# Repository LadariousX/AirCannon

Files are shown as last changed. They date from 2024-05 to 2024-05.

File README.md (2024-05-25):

# AirCannon
Repo for my recent air cannon project.



https://github.com/LadariousX/AirCannon/assets/42398415/c019e453-44b1-493c-81a6-e544174ef49f

This project is not for beginners... I'm no expert and I'm able to tell you not eveything went perfectly. I didnt even weld this one. That being said It came out nice but still you should have a strong basis in the followeing skills before attempting this project: Stainless welding (and other metalworking), 3d printing, CAD.

This project cost me near $300 R&D included your price will vary, heres the expenditures:
Don't forget to shop around these links are only reference!
| disc | 🔗 | 💰 | notes |
|---|---|----|---|
| Stainless fire extinguisher | 🧯 | 0.00 | recharge facility, out of cert |
| 1.5" full port ball valve | [link](https://www.directmaterial.com/brass-ball-valve-full-port-600-psi-wog) | 26.50 |
| 1.5 NPT x 10" pipe | [link](https://www.mcmaster.com/4549K664/) | 12.00 | 
| MH Build PETG | [link](https://www.matterhackers.com/store/c/3d-printer-filament/mh-build-series-petg) | 21.98 |ABS or machined lylon may work too|
| HM Build TPU | [link](https://www.matterhackers.com/store/c/mh-build-series-tpu)| 28.99 |
| 1/16" Coated steel cable | [link](https://www.homedepot.com/p/Everbilt-1-16-x-1-ft-Galvanized-Vinyl-Coated-Steel-Wire-Rope-in-Green-806376/204630484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) | 2.00 | Primary spring cable |
| (small) Coated steel cable | 🤷‍♂️ | 6.00| I used fishing leader|
| Misc Crimps | 🤷‍♂️ | 2.00 | cable crimps |
| 3/16" Brake line | 🤷‍♂️ | 10.00 | sleave for trigger linkage |
| Primary spring | 🤷‍♂️ | 🤪 | I slavaged mine from a dishwasher. |
| Trigger return spring | 🤷‍♂️ | 3.00 | choose to fit |
| Bering | [link](https://www.mcmaster.com/60355K336/) | 7.72 | McMasterCarr link... you can buy anywhere|
| .25 UNC x.75" socket head | [link](https://www.mcmaster.com/91274A164/) | 12.05 | Stainless not necessary but helps |
| .25" UNC nylon lock nut | [link](https://www.mcmaster.com/90715A125/) | 8.95 |
| M3x25 socket head | [link](https://www.mcmaster.com/91292A020/) | 8.72 |
| M3 nut | [link](https://www.mcmaster.com/91828A211/) | 4.73 |
| 1/4" NPT Guage| [link](https://www.mcmaster.com/4000K791-4000K565/) | 15.85 |
| Teflon / PTFE tape | [link](https://www.mcmaster.com/6802K33/) | 5.37 | 
| Misc air fittings | 🤷‍♂️ | 20.00 | m&f 1/4" NPT bung, valve, connector... |
| Por15 sealer | [link](https://por15.com/collections/fuel-tank-restoration/products/fuel-tank-sealer) | 18.38 | seal pinholes |

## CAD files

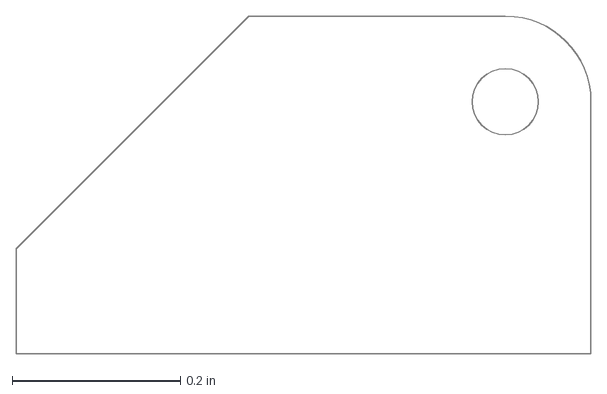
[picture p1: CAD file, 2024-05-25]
DXF cuts/125 rel spring anchor.dxf
0.684 x 0.402 in

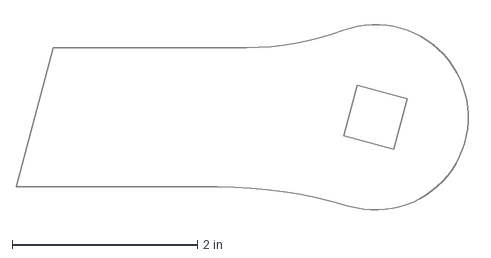
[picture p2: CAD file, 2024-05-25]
DXF cuts/furniture/125 Forwatd handle riser.dxf
4.95 x 2.17 in

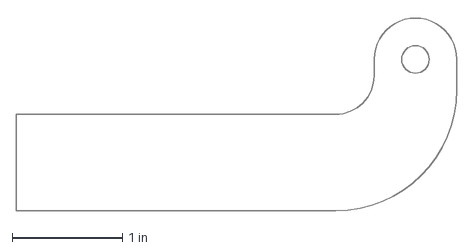
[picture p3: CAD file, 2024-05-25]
DXF cuts/rel sys/125 rel claw arm.dxf
4.00 x 1.77 in

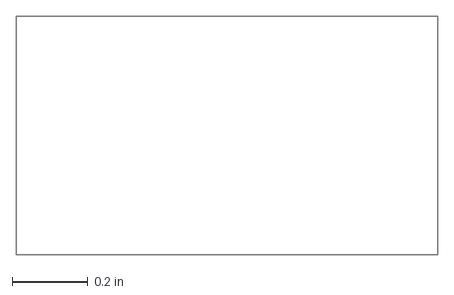
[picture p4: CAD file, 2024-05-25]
DXF cuts/tank inlet body/125 inlet back.dxf
1.11 x 0.63 in

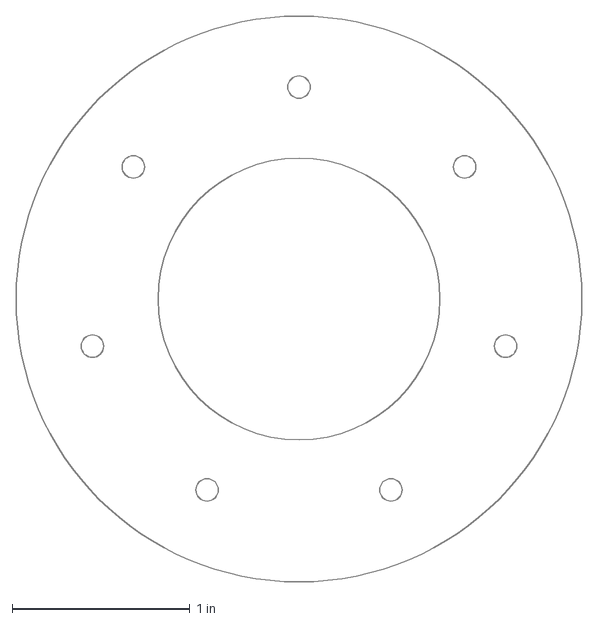
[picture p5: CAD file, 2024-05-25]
DXF cuts/trigger cam stack/16ga stack upper.dxf
3.19 x 3.19 in

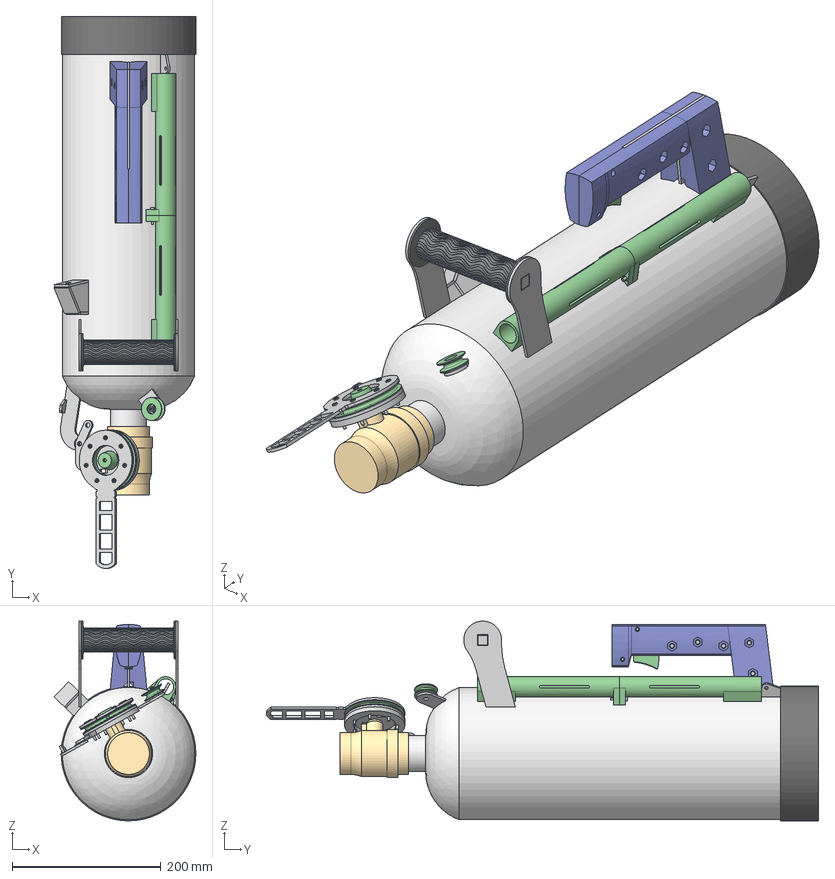
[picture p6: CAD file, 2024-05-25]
potato luancher Master.step
190.5 x 741.1 x 268.2 mm
inlet
hole saw align
Valve body
lower
track
Broached Hexagon Socket Head Cap Screw ANSI B18.3.1M - M3x0.5 x 25 St eel Grade 2 Zinc v1 x 7
trigger cam
arming lever
F handle riser L
F handle riser L(Mirror)
Socket Head Cap Screw JIS B 1176 - M3 x 0.5 x 20 Steel 4.6 Plain v1 x 2
spring anchor
handle body
trigger
Aft handle reinforcement
spacer
pully arm
spring pully
claw
Release arm
bushing
Hexagon Socket Head Cap Screw ANSI B18.3 - 1/4-28 UNF x 0.75 Steel Gr ade 2 Plain v1 x 5

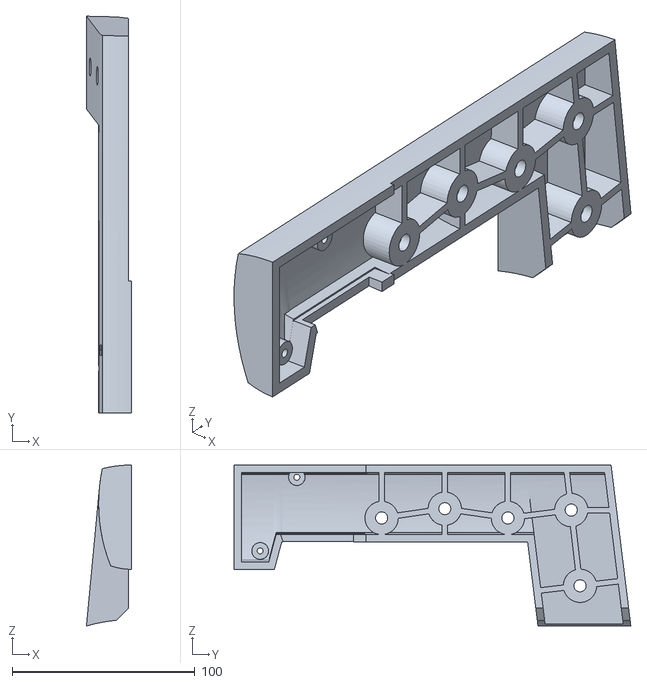
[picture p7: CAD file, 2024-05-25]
STL/aft handle/aft handle right.stl
24.7 x 216.9 x 88.0

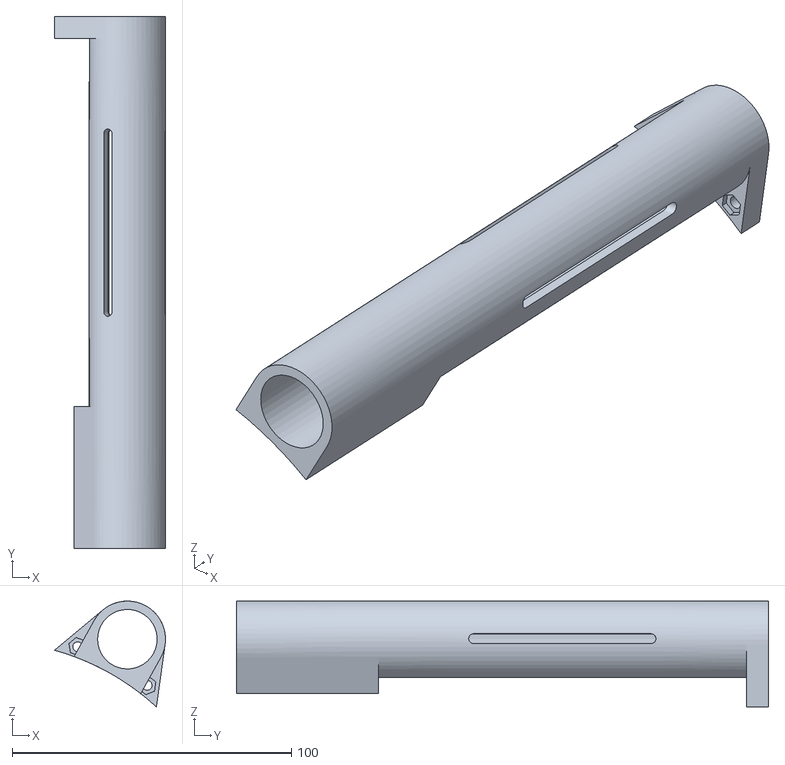
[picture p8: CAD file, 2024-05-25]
STL/buffer tube/buffer tube upper.stl
39.7 x 190.5 x 37.9

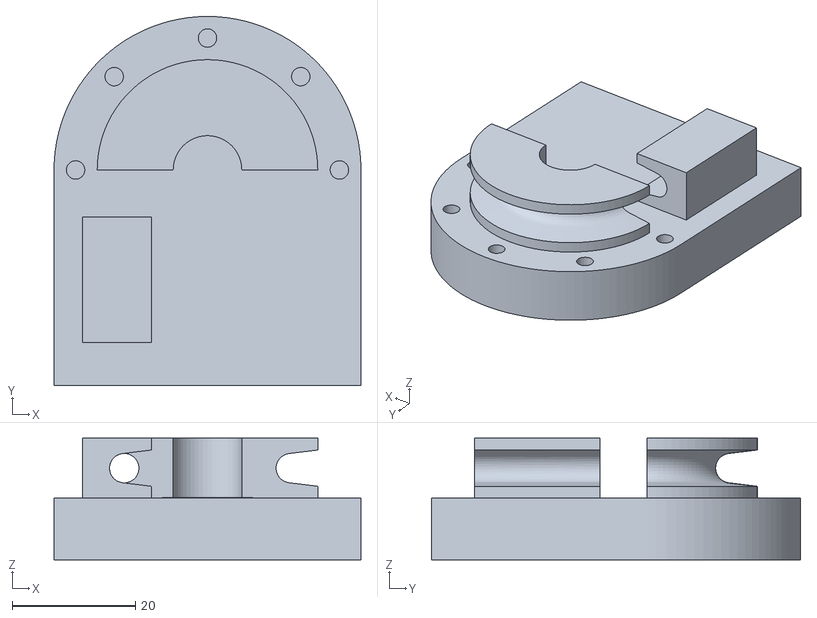
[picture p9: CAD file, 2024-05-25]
STL/jigs & alignment/tubing bender.stl
49.8 x 59.8 x 19.7

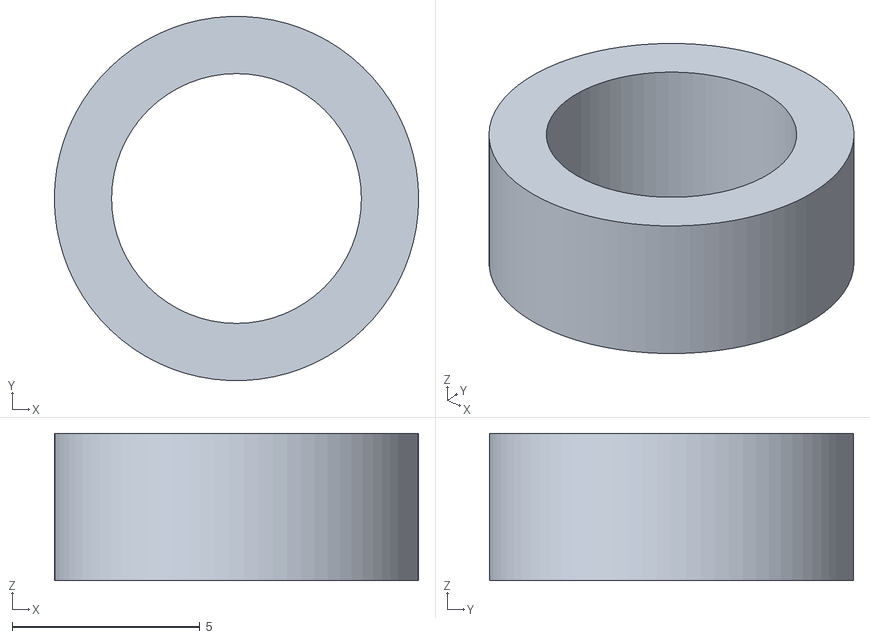
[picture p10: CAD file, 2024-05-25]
STL/Primary spring sys/primary pully 1 spacer.stl
9.70 x 9.69 x 3.91

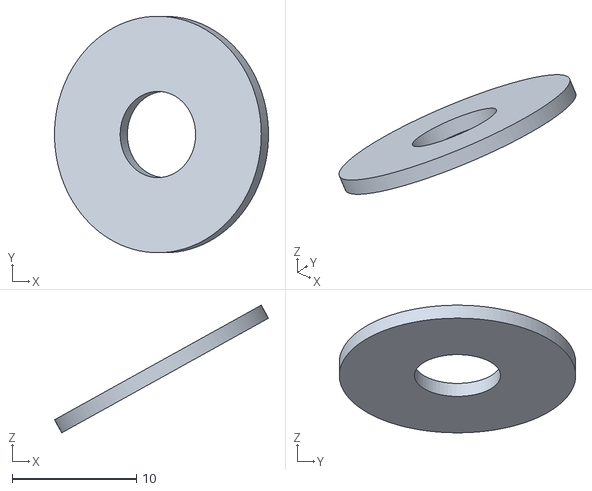
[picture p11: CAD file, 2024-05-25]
STL/rel claw bushing.stl
17.2 x 19.0 x 10.3

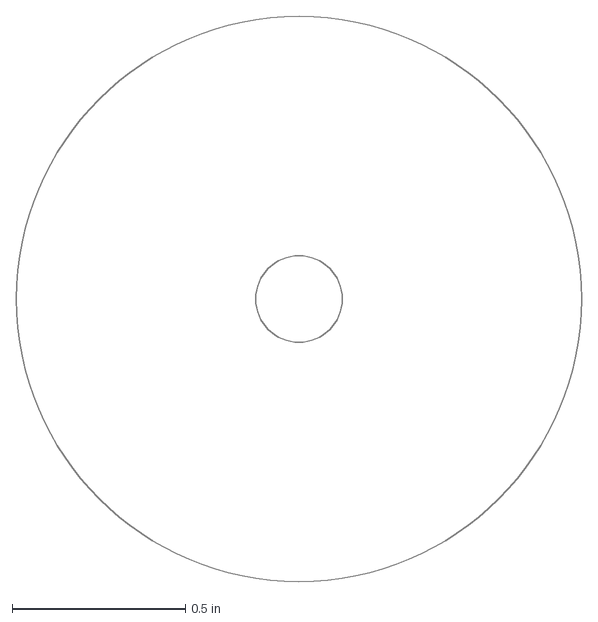
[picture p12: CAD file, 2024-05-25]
DXF cuts/125 hole saw align.dxf
1.63 x 1.63 in

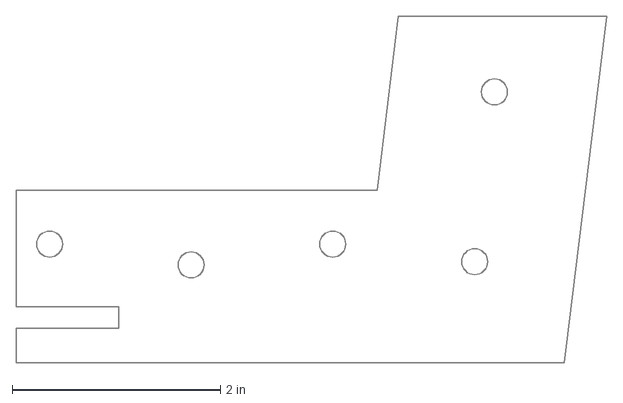
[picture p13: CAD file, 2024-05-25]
DXF cuts/furniture/125 aft handle reinf.dxf
5.67 x 3.33 in

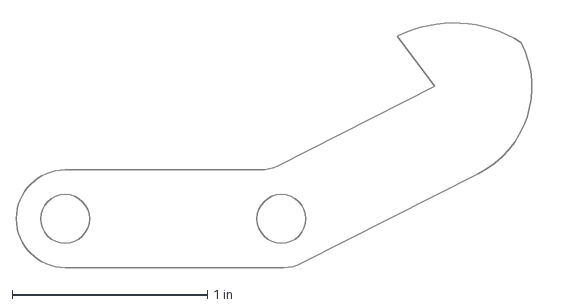
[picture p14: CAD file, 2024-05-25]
DXF cuts/rel sys/125 rel claw.dxf
2.71 x 1.29 in

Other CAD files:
DXF cuts/tank inlet body/125 inlet top.dxf
DXF cuts/trigger cam stack/125 stack lower.dxf
STL/aft handle/trigger.stl
STL/buffer tube/buffer tube lower.stl
DXF cuts/125 pully 1 arm.dxf
DXF cuts/125 spring anchor.dxf
DXF cuts/claw R1.dxf
DXF cuts/tank inlet body/125 inlet face.dxf
DXF cuts/tank inlet body/125 inlet side.dxf
DXF cuts/trigger cam stack/125 upper w handle.dxf
DXF cuts/trigger cam stack/25 stack trigger cam.dxf
STL/Primary spring sys/Primary cam.stl
STL/Primary spring sys/primary pully 1.stl
STL/aft handle/aft handle left.stl
STL/fwd handle grip.stl
STL/jigs & alignment/Aft reinf.stl
STL/jigs & alignment/Spring align.stl
STL/jigs & alignment/fwd handle align.stl
STL/jigs & alignment/inlet body jig.stl

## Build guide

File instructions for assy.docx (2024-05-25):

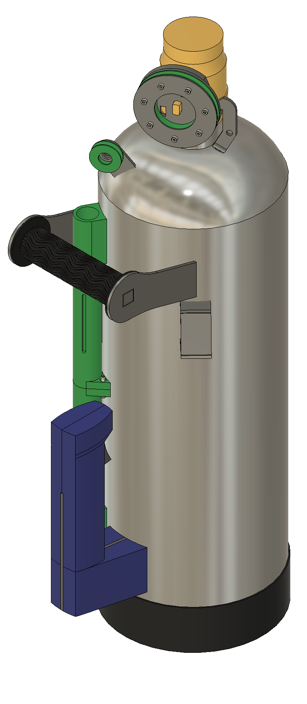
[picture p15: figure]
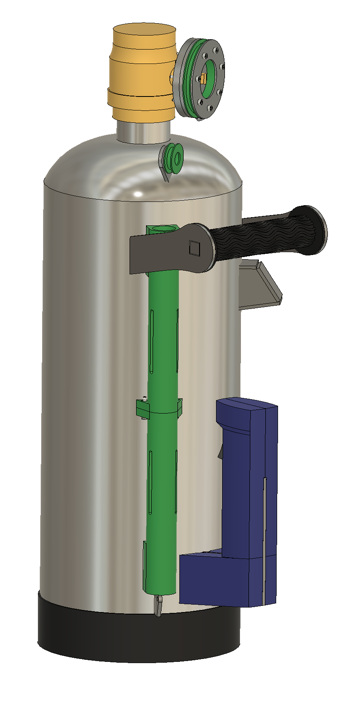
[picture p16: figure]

# Potato launcher instructions for assembly

Preferred order:

1. Outlet (threaded nipple)
2. Primary spring anchor
3. Forward handle
4. Valve body
5. Primary spring pully 1
6. Inlet body, position undetermined, ask me
7. Rear handle center plate

Take caution: anything made of plastic will melt at 475°F which doesn’t take very long to reach. At the same time, boiling plastic gas is inert.

Preference: don’t quench joints unless there is something melting or on fire as doing so compromises weld and material strength.

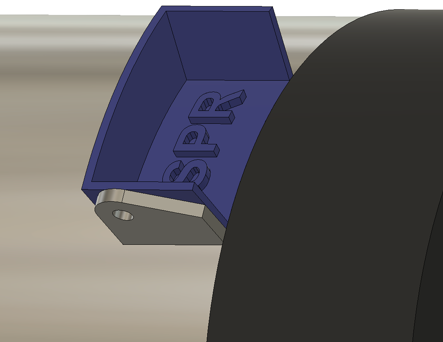
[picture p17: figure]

Alignment jigs are straight forward. They should have the same radius as the tank and one edge will align with the part and the other should be centered on the weld/seam of the tank which will be the centerline of the entire project. The jig for the rear handle though does not follow the centerline rule though of course since the plate itself will be on top of the seam.

Forward handle build

- Right off the bat void the quinch rule since the plate your welding is against the handle which is while it is a different type of plastic it still melts really quick.
- It may be easier to cut the square shaft connecting the two risers oversize since the joint will be ground flush anyways
- In regard to the lateral placement, if the distance from the top of the tank conflicts with the technical drawing, disregard the drawing

Primary spring system

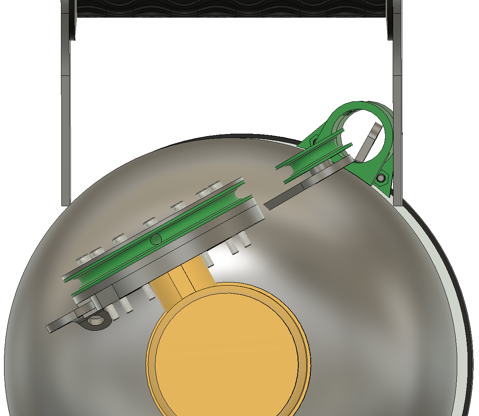
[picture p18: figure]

- When attaching pulleys related to the spring (trigger cam, pully 1) be sure that they are not only parallel but also that the center line that passes through them also passes through the main spring anchor
- The arm for Primary spring pully 1 is oversized and will need to be cut to length

Layden Blackwell 5/4/24
